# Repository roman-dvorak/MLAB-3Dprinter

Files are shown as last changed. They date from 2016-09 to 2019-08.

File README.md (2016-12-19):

RebeliX
=======
RebeliX – a 3D printer inspired by constructions of Rebel II a Prusa i3. Licensed as GPLv3. Howto and list of materials is available on www.RebeliX.cz (currently only in Czech, we are working on it, help is appreciated).

RebeliX Preview of assembled printer

Build
=====

   sudo pip install stlsort

To continue OpenSCAD has to be installed and available as `openscad` command.

1. Make necessary changes to configuration.scad according to printer that prints the parts and available hardware. 
* Generate a calibration object by `make calibration`.
* Print generated calibration.stl and repeat the steps if unhappy.

When satisfied, run `make clean && make all`. That produces STLs with your tweeks.

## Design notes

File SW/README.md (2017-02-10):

Configuration for Rebelix after editing for MLAB

Configuration.h used to generate printer firmware on these pages:
https://www.repetier.com/firmware/v092/index.php

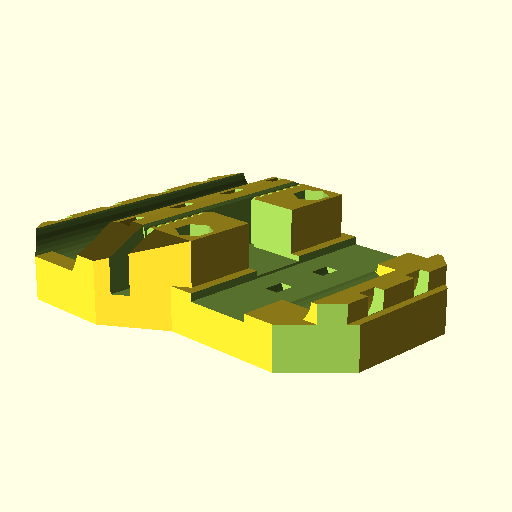
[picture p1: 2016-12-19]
images/x-carriage.png

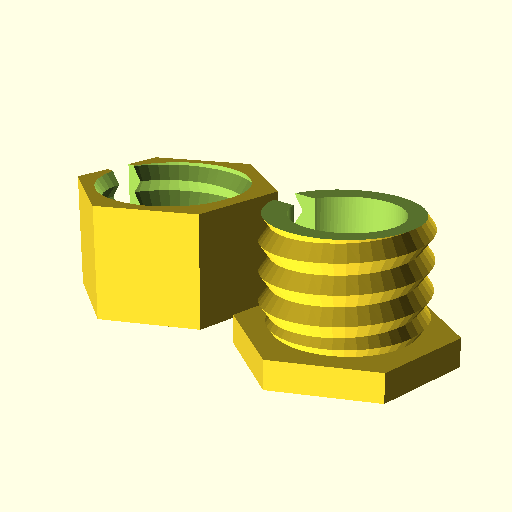
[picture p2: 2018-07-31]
images/filament_cleaner.png

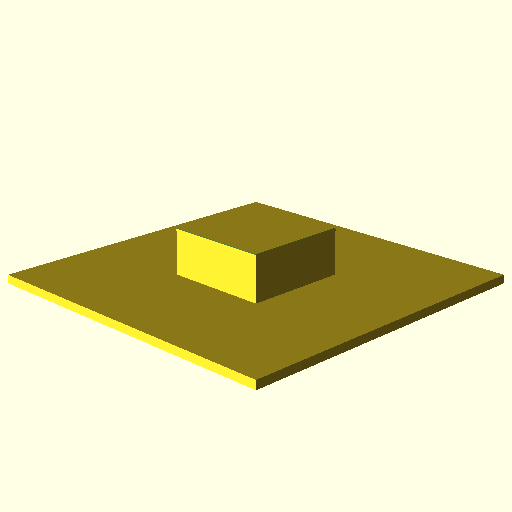
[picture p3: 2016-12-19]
images/profile-cover.png

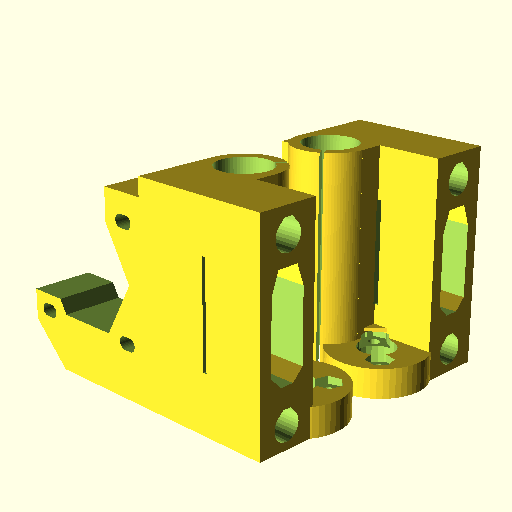
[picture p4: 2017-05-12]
images/x-end-motor.png

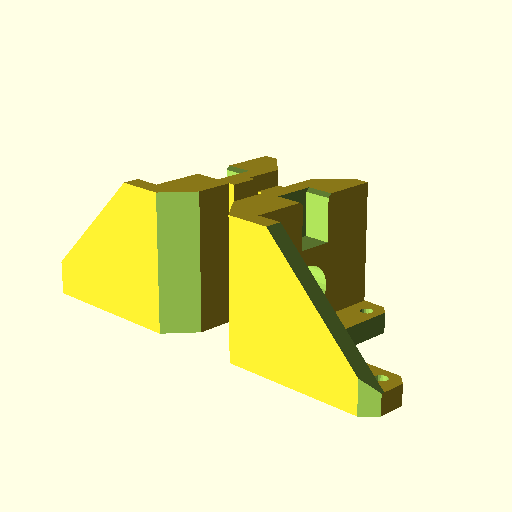
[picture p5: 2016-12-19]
images/z-bottom.png

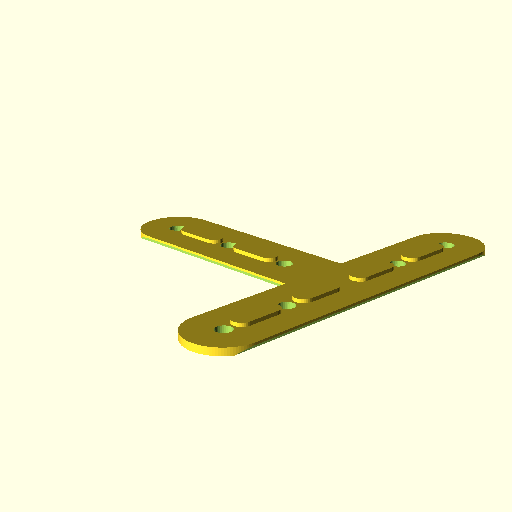
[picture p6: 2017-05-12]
images/z-coupler.png

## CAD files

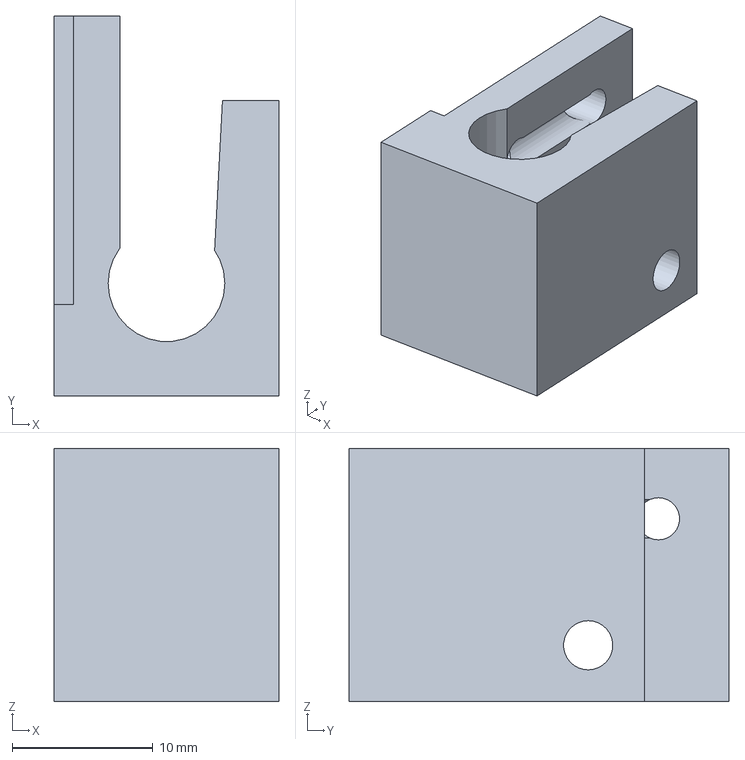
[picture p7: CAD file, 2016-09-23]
gcode/z-endstop-holder.amf
16.0 x 27.0 x 18.0 mm

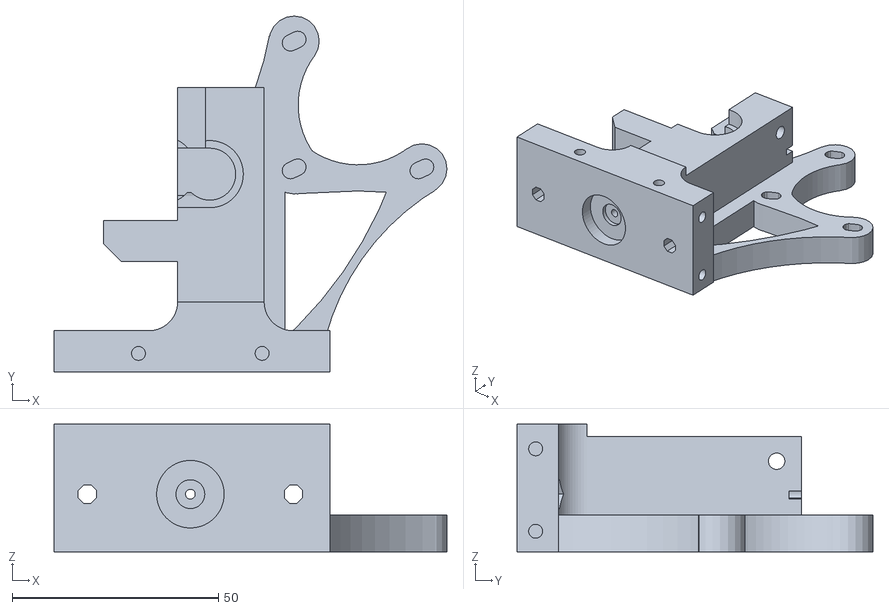
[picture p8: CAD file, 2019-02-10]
src/Extruder_filament_1.75mm/gregs-wade-625.stl
95.4 x 86.4 x 31.0

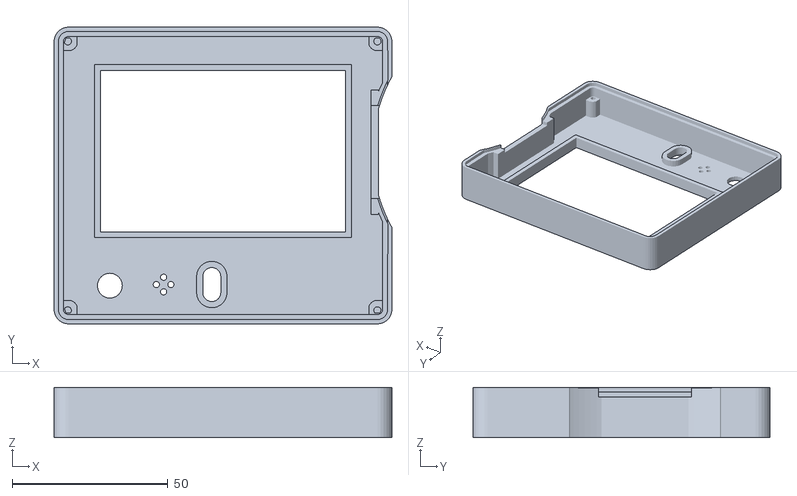
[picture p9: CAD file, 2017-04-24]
STL/LCD_holder/mods_for_display_case_front.stl
108.6 x 95.4 x 16.1

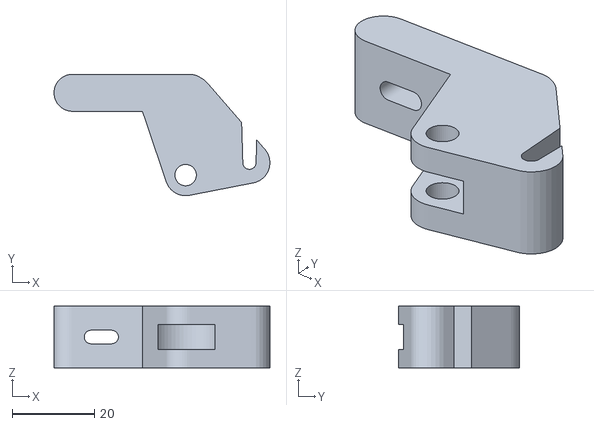
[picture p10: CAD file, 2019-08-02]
STL/MLAB_extruder/extruder_02.stl
52.5 x 29.5 x 15.0

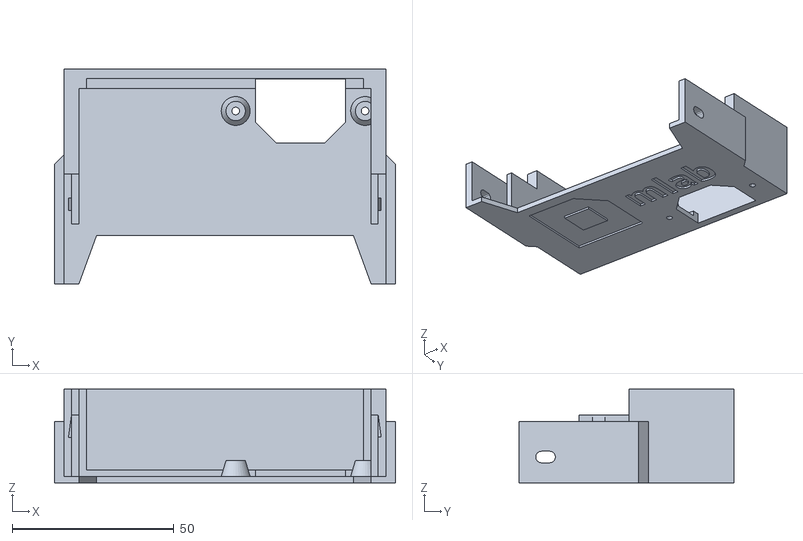
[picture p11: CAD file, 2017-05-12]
STL/Source_cover/Front_EURO_12V_240W.stl
105.4 x 66.5 x 29.0

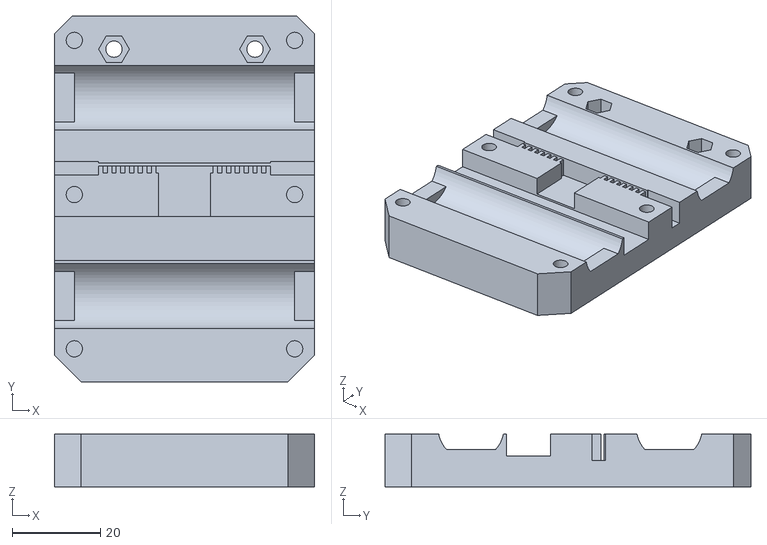
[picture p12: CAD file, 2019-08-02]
STL/x-carriage.stl
59.0 x 83.0 x 12.0

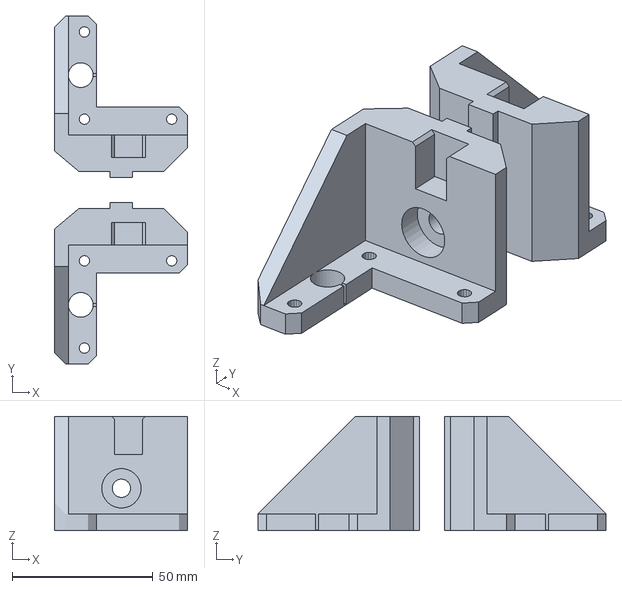
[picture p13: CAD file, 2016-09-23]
gcode/z-bottom.amf
47.3 x 123.6 x 40.6 mm

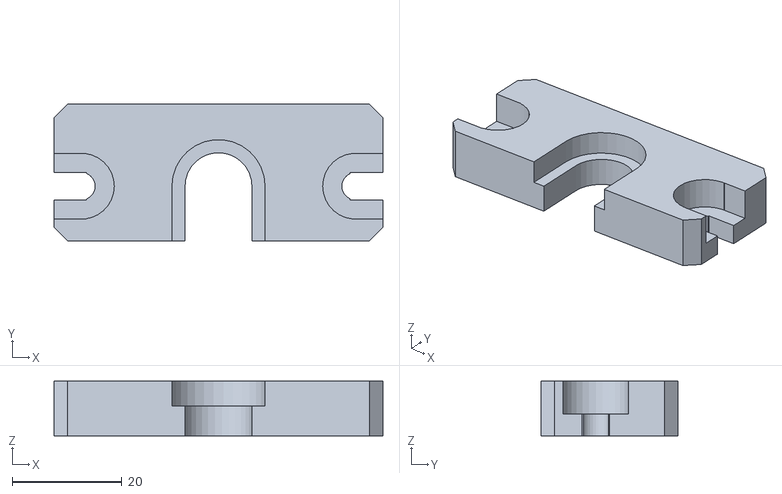
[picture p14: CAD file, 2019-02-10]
STL/Extruder_filament_1.75mm/j-head-mount.stl
60.0 x 25.0 x 10.0

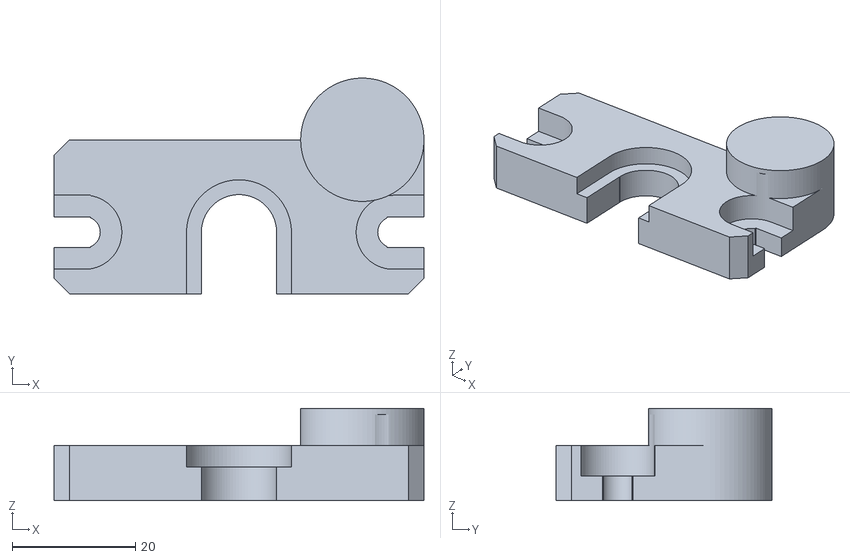
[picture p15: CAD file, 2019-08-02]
STL/j-head-mount.stl
60.0 x 35.0 x 15.0

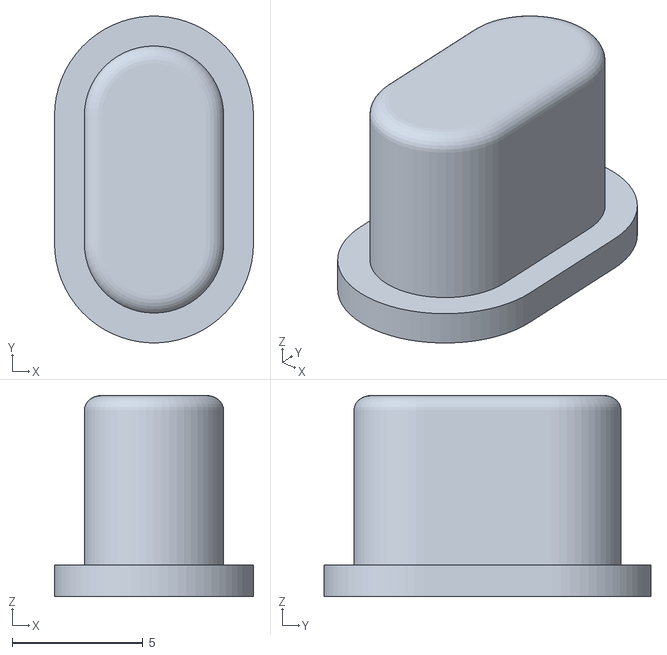
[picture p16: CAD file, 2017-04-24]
STL/LCD_holder/mods_for_display_case_button.stl
7.60 x 12.5 x 7.68

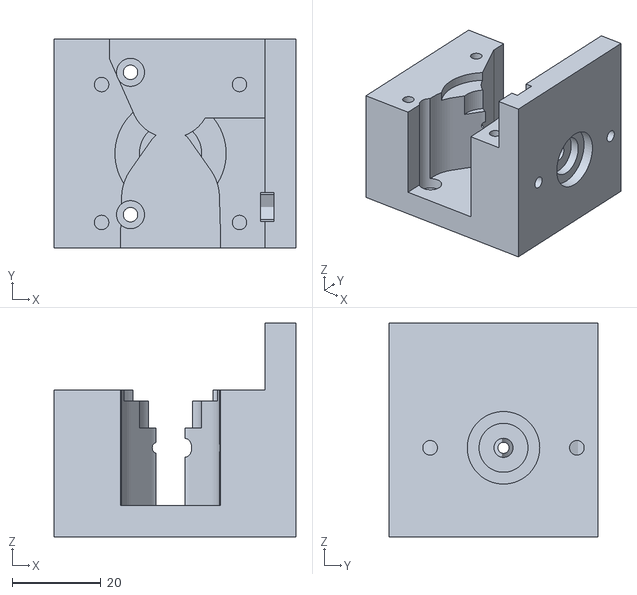
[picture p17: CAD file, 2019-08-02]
STL/MLAB_extruder/extruder_01.stl
54.4 x 46.9 x 48.0

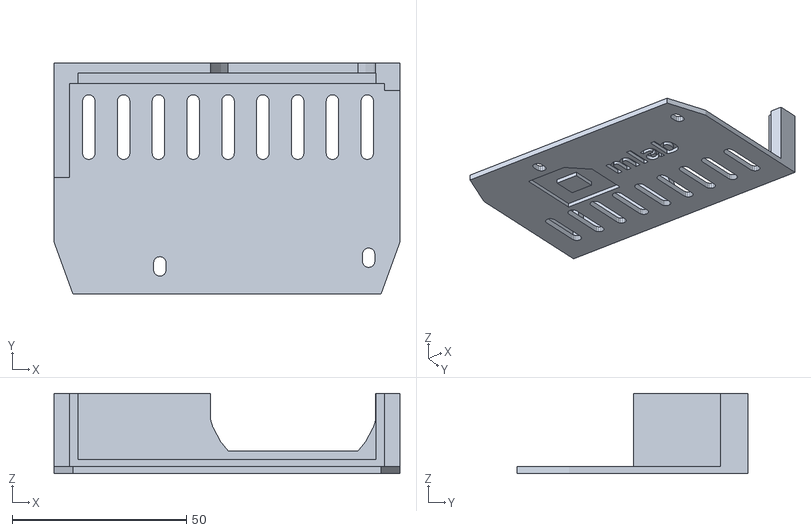
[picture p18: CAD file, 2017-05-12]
STL/Source_cover/Rear_EURO_12V_240W.stl
99.4 x 66.5 x 23.0

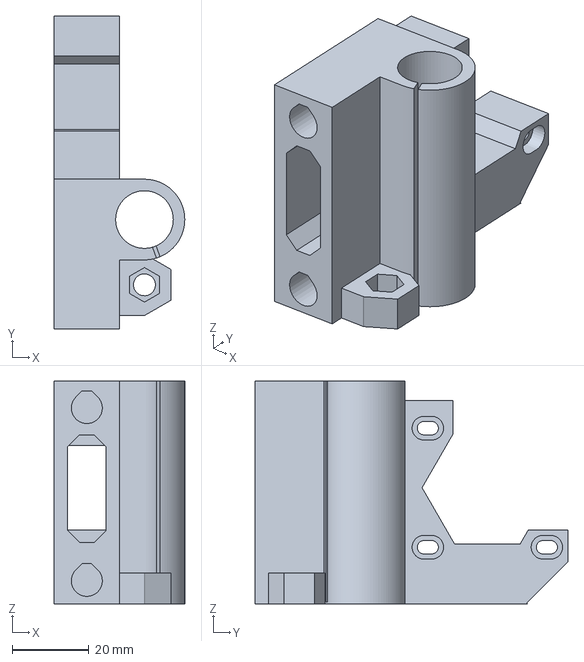
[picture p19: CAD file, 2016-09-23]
gcode/x-end-motor.amf
34.0 x 81.5 x 58.0 mm

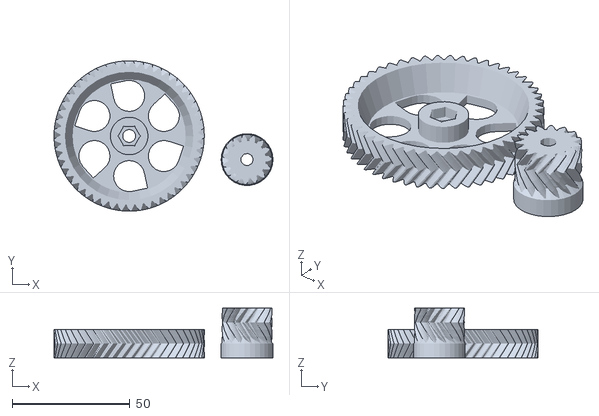
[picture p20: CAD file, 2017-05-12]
STL/Extruder_filament_1.75mm/wade-gears.stl
92.9 x 63.7 x 21.0

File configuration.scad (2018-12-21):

// Layer high for the printing [mm]
layer_height = 0.20; //Slic3r->Print Settings->Layers and perimeters->Layer height

// Spare for the screws heads [mm]
spare = 0.75;
// M6 screw diameter [mm]
M6_head_diameter = 13.6+spare;
//M6_head_diameter = 10.6+spare;
//M6_head_diameter = 12+spare;

// M6 head high (for hiding it) [mm]
//M6_head_height = 4;
M6_head_height = 3.6;
//M6_head_height = 4.5;

// Screws and rods diameters
M8_smooth_rod_diameter = 8.3;
M8_smooth_rod_diameter_catch = 8.4;
// Prumer 8mm tyce
rod_8mm_d = 8.2; //pro dil z-top
M6_diameter = 6.6;
M6_dia=M6_diameter; //pro dil z-top
M6_diamater_horizontal = 6.5;
M3_diameter = 3.7;
M3_diameter_horizontal = 3.5;

//matice trapézové tyče
TRAP_diameter_externa=22; //průmer vnější


// Nuts diameters
M3_nut_diameter = 7.0;
M3_nut_diameter_horizontal = 6.7;

// ALU profile parameters
ALU_cut_width = 7.9;
ALU_cut_width_horizontal = 7.7;

// Sirka matky do profilu (pokud neni pouzita, tak 0)
profile_nut_width = 10;
//profile_nut_width = 0; //pro z-top

// Motors length/depth (for axes Z and Y)
//SX17-1003LQFE (recommended for the Z axis)
motor_length = 29.5;
//SX17-1003 (recommended for the Z axis)
//motor_length = 34;
//SX17-1005
//motor_length = 40;
//SX17-0905 - this motor is too high - the Z end stop holder has to be adjusted
//motor_length = 48;

// Extrusion width [mm]
extrusion_width = 0.66; //Slic3r->Print Settings->Advanced->Default extrusion width

/// Belt type ******************************************************

// GT2
belt_tooth_distance = 2;
belt_tooth_ratio = 0.5;
belt_tooth_height = 1.4;
belt_thickness = 2.3;


// T2.5
//belt_tooth_distance = 2.5;
//belt_tooth_ratio = 0.68;

// Z screw......



// Tloustka rohovych spojek
// 5 mm => sroub M6x14 s podlozkou
// 3 mm => sroub M6x12 s podlozkou
coupler_thickness = 3;

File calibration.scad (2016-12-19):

include <./configuration.scad>

difference(){
	union(){
		cube([36,30,5]);
		translate([0,23,0])cube([35,10,25]);
		translate([M6_diameter*2+8,20,0])cube([ALU_cut_width_horizontal,11,20]);
	}
	translate([M6_diameter,M6_diameter+M3_diameter+5,-1])cylinder(r=M6_diameter/2,h=7,$fn=32);
	translate([M6_diameter,M3_diameter+2,-1]){
		cylinder(r=M3_diameter/2,h=7,$fn=16);	
		translate([0,0,3.5])cylinder(r=M3_nut_diameter/2,h=2.6,$fn=6);
	}
	translate([M6_diameter+M8_smooth_rod_diameter,M8_smooth_rod_diameter+3,layer_height])cylinder(h=7,r=M8_smooth_rod_diameter_catch/2,$fn = 30);
	translate([34.5,M8_smooth_rod_diameter+3,-1])cylinder(h=7,r=M8_smooth_rod_diameter/2,$fn = 30);
	
	translate([M6_diameter+4,34,10]) 
	rotate([90,0,0]){
		cylinder(h = 15, r=M3_diameter_horizontal/2, $fn=30);
		cylinder(h = 4, r=M3_nut_diameter_horizontal/2, $fn=6);
	}

	translate([M6_diameter*2+8+ALU_cut_width/2,34,12]) 
	rotate([90,0,0]){
		cylinder(r = M6_diamater_horizontal/2, h = 15, $fn = 30);
		cylinder(r = M6_head_diameter/2, h = 4, $fn = 30);
	}
	
	translate([-1,27,18.5])belt_holder_beltcut();
}

translate([M6_diameter*2+8,0,0])cube([ALU_cut_width,M6_diameter*2+8,7]);

module belt_holder_beltcut(){
 echo(belt_tooth_ratio*belt_tooth_distance);
 position_tweak=-1.1;
 // Belt slit
 //translate([-66,-0.5+10,3]) 
 translate([0,1.5,0])
 cube([67,0.8,15]);
 // Smooth insert cutout
 //translate([-66,-0.5+10,12]) 
 translate([0,1.5,5])
 rotate([45,0,0]) cube([67,15,15]);
 // Individual teeth
 for ( i = [0 : 23] ){
 	translate([0+i*belt_tooth_distance+position_tweak,0,0]) cube([belt_tooth_ratio*belt_tooth_distance,1.7,15]);
 }
}

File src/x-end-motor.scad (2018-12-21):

    // PRUSA iteration3
// x end motor
// GNU GPL v3
// Josef Průša <iam@josefprusa.cz> and contributors
// http://www.reprap.org/wiki/Prusa_Mendel
// http://prusamendel.org


z_thread_diameter = 12;

include <../configuration.scad>
use <inc/x-end.scad>

module x_end_motor_base(){
 x_end_base();
 translate(v=[-15,31,26.5]) cube(size = [17,44,53], center = true);
}

module x_end_motor_holes(){
 x_end_holes();
 // Position to place
 translate(v=[-1,32,30.25]){
  // Belt hole
  translate(v=[-14,1,0]) cube(size = [10,46,22], center = true);
  // Motor mounting holes
  //translate(v=[20,-15.5,-15.5]) rotate(a=[0,-90,0]) rotate(a=[0,0,90]) cylinder(h = 70, r=1.8, $fn=30);
  //translate(v=[1,-15.5,-15.5]) rotate(a=[0,-90,0]) rotate(a=[0,0,90]) cylinder(h = 10, r=3.1, $fn=30);

  hull(){
    translate(v=[20,-16.5,-15.5]) rotate(a=[0,-90,0]) rotate(a=[0,0,90]) cylinder(h = 70, r=M3_diameter_horizontal/2, $fn=30);
    translate(v=[20,-14.5,-15.5]) rotate(a=[0,-90,0]) rotate(a=[0,0,90]) cylinder(h = 70, r=M3_diameter_horizontal/2, $fn=30);
  }
  hull(){
    translate(v=[1,-16.5,-15.5]) rotate(a=[0,-90,0]) rotate(a=[0,0,90]) cylinder(h = 10, r=3.1, $fn=30);
    translate(v=[1,-14.5,-15.5]) rotate(a=[0,-90,0]) rotate(a=[0,0,90]) cylinder(h = 10, r=3.1, $fn=30);
  }

  hull(){
    translate(v=[20,-16.5,15.5]) rotate(a=[0,-90,0]) rotate(a=[0,0,90]) cylinder(h = 70, r=M3_diameter_horizontal/2, $fn=30);
    translate(v=[20,-14.5,15.5]) rotate(a=[0,-90,0]) rotate(a=[0,0,90]) cylinder(h = 70, r=M3_diameter_horizontal/2, $fn=30);
  }
  hull(){
    translate(v=[1,-16.5,15.5]) rotate(a=[0,-90,0]) rotate(a=[0,0,90]) cylinder(h = 10, r=3.1, $fn=30);
    translate(v=[1,-14.5,15.5]) rotate(a=[0,-90,0]) rotate(a=[0,0,90]) cylinder(h = 10, r=3.1, $fn=30);
  }

  hull(){
    translate(v=[20,16.5,-15.5]) rotate(a=[0,-90,0]) rotate(a=[0,0,90]) cylinder(h = 70, r=M3_diameter_horizontal/2, $fn=30);
    translate(v=[20,14.5,-15.5]) rotate(a=[0,-90,0]) rotate(a=[0,0,90]) cylinder(h = 70, r=M3_diameter_horizontal/2, $fn=30);
  }
  hull(){
    translate(v=[1,16.5,-15.5]) rotate(a=[0,-90,0]) rotate(a=[0,0,90]) cylinder(h = 10, r=3.1, $fn=30);
    translate(v=[1,14.5,-15.5]) rotate(a=[0,-90,0]) rotate(a=[0,0,90]) cylinder(h = 10, r=3.1, $fn=30);
  }

  // Material saving cutout
  translate(v=[-10,12,10]) cube(size = [60,42,42], center = true);

  // Material saving cutout
  translate(v=[-10,40,-30]) rotate(a=[45,0,0])  cube(size = [60,42,42], center = true);
  // Motor shaft cutout
  translate(v=[0,0,0]) rotate(a=[0,-90,0]) rotate(a=[0,0,90+180/8]) cylinder(h = 70, r=17, $fn=8);
  // without motor
  translate(v=[0,-19,0]) rotate(a=[0,-90,0]) rotate(a=[0,0,90]) cylinder(h = 70, d=M3_diameter_horizontal, $fn=60);
  translate(v=[5,-19,0]) rotate(a=[0,-90,0]) rotate(a=[0,0,0]) cylinder(h = 5+8, d=6.4, $fn=6);
  translate(v=[-20,-19,0]) rotate(a=[0,-90,0]) rotate(a=[0,0,0]) cylinder(h = 5+8, d=6.1, $fn=30);
 }
}

// Final part
module x_end_motor(){
 difference(){
  x_end_motor_base();
  x_end_motor_holes();
 }

 translate([30,0,0]) mirror([1,0,0])
   difference(){
   x_end_motor_base();
   x_end_motor_holes();
 }
}

x_end_motor();

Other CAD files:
STL/Extruder_filament_1.75mm/gregs-wade-625.stl
STL/LCD_holder/mods_for_display_case_back.stl
STL/MLAB_extruder/extruder_04.stl
STL/x-carriage-back.stl
src/y-motor.scad
STL/Extruder_filament_1.75mm/extruder-idler.stl
STL/Extruder_filament_1.75mm/extruder-washer.stl
STL/Extruder_filament_1.75mm/extruder_fan.stl
STL/M6_nut_case/M6-case-corner.stl
STL/M6_nut_case/M6-case-dual.stl
STL/M6_nut_case/M6-case-simple.stl
STL/RAMPS_mini.stl
STL/cable-holder-Nema17.stl
STL/cable-holder.stl
STL/corner-coupler.stl
STL/filament_cleaner.stl
STL/heatbed-nut.stl
STL/profile-cover-hole.stl
STL/profile-cover.stl
STL/spool-center.stl
STL/spool-holder.stl
STL/spool_bearing.stl
STL/x-end-motor.stl
STL/y-LM8UU-holder.stl
STL/y-belt-holder.stl
STL/y-motor.stl
STL/y-rod-holder.stl
STL/z-bottom.stl
STL/z-coupler.stl
STL/z-endstop-holder.stl
STL/z-endstop-piezo.stl
STL/z-top.stl
gcode/cable-holder.amf
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

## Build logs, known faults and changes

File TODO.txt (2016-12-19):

Optimalizace modelu pro tisk 

Vyhladit model ozubenych kol. Zvazit modifikaci zubu kola, tak aby nevznikal pri tisku otrep v ozubeni. 

Nastaveni tisku

Snizit mnozstvi vyplne na cca 20%. Asi pouzivat spis typ vyplne Honeycomp, nez reclinear. Honeykomb ma zda se vetsi prispevek k pevnosti.

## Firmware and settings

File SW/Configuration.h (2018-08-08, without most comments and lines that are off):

#define CONFIGURATION_H
#define NUM_EXTRUDER 1
#define MOTHERBOARD 33
#include "pins.h"
#undef FAN_PIN
#define FAN_PIN 9
#undef FAN_BOARD_PIN
#define FAN_BOARD_PIN -1
#define BOARD_FAN_SPEED 255
#define FAN_THERMO_PIN -1
#define FAN_THERMO_MIN_PWM 128
#define FAN_THERMO_MAX_PWM 255
#define FAN_THERMO_MIN_TEMP 45
#define FAN_THERMO_MAX_TEMP 60
#define FAN_THERMO_THERMISTOR_PIN -1
#define FAN_THERMO_THERMISTOR_TYPE 1
#define BLUETOOTH_SERIAL  -1
#define BLUETOOTH_BAUD  115200
#define MIXING_EXTRUDER 0
#define DRIVE_SYSTEM 0
#define XAXIS_STEPS_PER_MM 80
#define YAXIS_STEPS_PER_MM 80
#define ZAXIS_STEPS_PER_MM 408.15
#define EXTRUDER_FAN_COOL_TEMP 50
#define PDM_FOR_EXTRUDER 0
#define PDM_FOR_COOLER 0
#define DECOUPLING_TEST_MAX_HOLD_VARIANCE 20
#define DECOUPLING_TEST_MIN_TEMP_RISE 1
#define KILL_IF_SENSOR_DEFECT 0
#define RETRACT_ON_PAUSE 2
#define PAUSE_START_COMMANDS ""
#define PAUSE_END_COMMANDS ""
#define SHARED_EXTRUDER_HEATER 0
#define EXT0_X_OFFSET 0
#define EXT0_Y_OFFSET 0
#define EXT0_Z_OFFSET 0
#define EXT0_STEPS_PER_MM 514
#define EXT0_TEMPSENSOR_TYPE 14
#define EXT0_TEMPSENSOR_PIN TEMP_0_PIN
#define EXT0_HEATER_PIN HEATER_0_PIN
#define EXT0_STEP_PIN ORIG_E0_STEP_PIN
#define EXT0_DIR_PIN ORIG_E0_DIR_PIN
#define EXT0_INVERSE 1
#define EXT0_ENABLE_PIN ORIG_E0_ENABLE_PIN
#define EXT0_ENABLE_ON 0
#define EXT0_MIRROR_STEPPER 0
#define EXT0_STEP2_PIN ORIG_E0_STEP_PIN
#define EXT0_DIR2_PIN ORIG_E0_DIR_PIN
#define EXT0_INVERSE2 0
#define EXT0_ENABLE2_PIN ORIG_E0_ENABLE_PIN
#define EXT0_MAX_FEEDRATE 50
#define EXT0_MAX_START_FEEDRATE 20
#define EXT0_MAX_ACCELERATION 1000
#define EXT0_HEAT_MANAGER 3
#define EXT0_WATCHPERIOD 1
#define EXT0_PID_INTEGRAL_DRIVE_MAX 250
#define EXT0_PID_INTEGRAL_DRIVE_MIN 100
#define EXT0_PID_PGAIN_OR_DEAD_TIME 2
#define EXT0_PID_I 6
#define EXT0_PID_D 40
#define EXT0_PID_MAX 255
#define EXT0_ADVANCE_K 0
#define EXT0_ADVANCE_L 0
#define EXT0_ADVANCE_BACKLASH_STEPS 0
#define EXT0_WAIT_RETRACT_TEMP 150
#define EXT0_WAIT_RETRACT_UNITS 0
#define EXT0_SELECT_COMMANDS ""
#define EXT0_DESELECT_COMMANDS ""
#define EXT0_EXTRUDER_COOLER_PIN 8
#define EXT0_EXTRUDER_COOLER_SPEED 255
#define EXT0_DECOUPLE_TEST_PERIOD 12000
#define EXT0_JAM_PIN -1
#define EXT0_JAM_PULLUP 0
#define FEATURE_RETRACTION 1
#define AUTORETRACT_ENABLED 0
#define RETRACTION_LENGTH 3
#define RETRACTION_LONG_LENGTH 13
#define RETRACTION_SPEED 40
#define RETRACTION_Z_LIFT 0
#define RETRACTION_UNDO_EXTRA_LENGTH 0
#define RETRACTION_UNDO_EXTRA_LONG_LENGTH 0
#define RETRACTION_UNDO_SPEED 20
#define FILAMENTCHANGE_X_POS 0
#define FILAMENTCHANGE_Y_POS 0
#define FILAMENTCHANGE_Z_ADD  2
#define FILAMENTCHANGE_REHOME 1
#define FILAMENTCHANGE_SHORTRETRACT 5
#define FILAMENTCHANGE_LONGRETRACT 50
#define JAM_STEPS 220
#define JAM_SLOWDOWN_STEPS 320
#define JAM_SLOWDOWN_TO 70
#define JAM_ERROR_STEPS 500
#define JAM_MIN_STEPS 10
#define JAM_ACTION 1
#define RETRACT_DURING_HEATUP true
#define PID_CONTROL_RANGE 10
#define SKIP_M109_IF_WITHIN 2
#define SCALE_PID_TO_MAX 0
#define TEMP_HYSTERESIS 0
#define EXTRUDE_MAXLENGTH 160
#define NUM_TEMPS_USERTHERMISTOR0 0
#define USER_THERMISTORTABLE0 {}
#define NUM_TEMPS_USERTHERMISTOR1 0
#define USER_THERMISTORTABLE1 {}
#define NUM_TEMPS_USERTHERMISTOR2 0
#define USER_THERMISTORTABLE2 {}
#define GENERIC_THERM_VREF 5
#define GENERIC_THERM_NUM_ENTRIES 33
#define HEATER_PWM_SPEED 0
#define HAVE_HEATED_BED 0
#define HEATED_BED_MAX_TEMP 120
#define SKIP_M190_IF_WITHIN 3
#define HEATED_BED_SENSOR_TYPE 14
#define HEATED_BED_SENSOR_PIN TEMP_1_PIN
#define HEATED_BED_HEATER_PIN HEATER_1_PIN
#define HEATED_BED_SET_INTERVAL 5000
#define HEATED_BED_HEAT_MANAGER 3
#define HEATED_BED_PID_INTEGRAL_DRIVE_MAX 255
#define HEATED_BED_PID_INTEGRAL_DRIVE_MIN 80
#define HEATED_BED_PID_PGAIN_OR_DEAD_TIME   2
#define HEATED_BED_PID_IGAIN   18.38
#define HEATED_BED_PID_DGAIN 530.16
#define HEATED_BED_PID_MAX 255
#define HEATED_BED_DECOUPLE_TEST_PERIOD 300000
#define MIN_EXTRUDER_TEMP 150
#define MAXTEMP 248
#define MIN_DEFECT_TEMPERATURE -30
#define MAX_DEFECT_TEMPERATURE 255
#define SUPPORT_LASER 0
#define LASER_PIN -1
#define LASER_ON_HIGH 1
#define SUPPORT_CNC 0
#define CNC_WAIT_ON_ENABLE 300
#define CNC_WAIT_ON_DISABLE 0
#define CNC_ENABLE_PIN -1
#define CNC_ENABLE_WITH 1
#define CNC_DIRECTION_PIN -1
#define CNC_DIRECTION_CW 1
#define DEFAULT_PRINTER_MODE 0
#define ENDSTOP_PULLUP_X_MIN true
#define ENDSTOP_X_MIN_INVERTING false
#define MIN_HARDWARE_ENDSTOP_X true
#define ENDSTOP_PULLUP_Y_MIN true
#define ENDSTOP_Y_MIN_INVERTING false
#define MIN_HARDWARE_ENDSTOP_Y true
#define ENDSTOP_PULLUP_Z_MIN false
#define ENDSTOP_Z_MIN_INVERTING true
#define MIN_HARDWARE_ENDSTOP_Z true
#define ENDSTOP_PULLUP_X_MAX true
#define ENDSTOP_X_MAX_INVERTING false
#define MAX_HARDWARE_ENDSTOP_X false
#define ENDSTOP_PULLUP_Y_MAX true
#define ENDSTOP_Y_MAX_INVERTING false
#define MAX_HARDWARE_ENDSTOP_Y false
#define ENDSTOP_PULLUP_Z_MAX true
#define ENDSTOP_Z_MAX_INVERTING false
#define MAX_HARDWARE_ENDSTOP_Z false
#define max_software_endstop_r true
#define min_software_endstop_x false
#define min_software_endstop_y false
#define min_software_endstop_z false
#define max_software_endstop_x true
#define max_software_endstop_y true
#define max_software_endstop_z true
#define ENDSTOP_X_BACK_MOVE 5
#define ENDSTOP_Y_BACK_MOVE 5
#define ENDSTOP_Z_BACK_MOVE 10
#define ENDSTOP_X_RETEST_REDUCTION_FACTOR 2
#define ENDSTOP_Y_RETEST_REDUCTION_FACTOR 2
#define ENDSTOP_Z_RETEST_REDUCTION_FACTOR 0
#define ENDSTOP_X_BACK_ON_HOME 1
#define ENDSTOP_Y_BACK_ON_HOME 1
#define ENDSTOP_Z_BACK_ON_HOME 0
#define ALWAYS_CHECK_ENDSTOPS 1
#define X_ENABLE_ON 0
#define Y_ENABLE_ON 0
#define Z_ENABLE_ON 0
#define DISABLE_X 0
#define DISABLE_Y 0
#define DISABLE_Z 1
#define DISABLE_E 0
#define INVERT_X_DIR 0
#define INVERT_Y_DIR 1
#define INVERT_Z_DIR 0
#define X_HOME_DIR -1
#define Y_HOME_DIR -1
#define Z_HOME_DIR -1
#define X_MAX_LENGTH 185
#define Y_MAX_LENGTH 180
#define Z_MAX_LENGTH 185
#define X_MIN_POS 0
#define Y_MIN_POS 0
#define Z_MIN_POS 0
#define DISTORTION_CORRECTION 1
#define DISTORTION_CORRECTION_POINTS 5
#define DISTORTION_CORRECTION_R 100
#define DISTORTION_PERMANENT 1
#define DISTORTION_UPDATE_FREQUENCY 15
#define DISTORTION_START_DEGRADE 0.5
#define DISTORTION_END_HEIGHT 1
#define DISTORTION_EXTRAPOLATE_CORNERS 0
#define DISTORTION_XMIN 10
#define DISTORTION_YMIN 10
#define DISTORTION_XMAX 190
#define DISTORTION_YMAX 190
#define FEATURE_BABYSTEPPING 1
#define BABYSTEP_MULTIPLICATOR 80
#define DELTA_SEGMENTS_PER_SECOND_PRINT 180 // Move accurate setting for print moves
#define DELTA_SEGMENTS_PER_SECOND_MOVE 70 // Less accurate setting for other moves
#define EXACT_DELTA_MOVES 1
#define DELTA_HOME_ON_POWER 0
#define DELTASEGMENTS_PER_PRINTLINE 24
#define STEPPER_INACTIVE_TIME 360L
#define MAX_INACTIVE_TIME 0L
#define MAX_FEEDRATE_X 80
#define MAX_FEEDRATE_Y 80
#define MAX_FEEDRATE_Z 30
#define HOMING_FEEDRATE_X 50
#define HOMING_FEEDRATE_Y 50
#define HOMING_FEEDRATE_Z 15
#define HOMING_ORDER HOME_ORDER_XYZ
#define ZHOME_MIN_TEMPERATURE 0
#define ZHOME_HEAT_ALL 1
#define ZHOME_HEAT_HEIGHT 20
#define ZHOME_X_POS 999999
#define ZHOME_Y_POS 999999
#define ENABLE_BACKLASH_COMPENSATION 0
#define X_BACKLASH 0
#define Y_BACKLASH 0
#define Z_BACKLASH 0
#define RAMP_ACCELERATION 1
#define STEPPER_HIGH_DELAY 1
#define DIRECTION_DELAY 0
#define STEP_DOUBLER_FREQUENCY 12000
#define ALLOW_QUADSTEPPING 1
#define DOUBLE_STEP_DELAY 1 // time in microseconds
#define MAX_ACCELERATION_UNITS_PER_SQ_SECOND_X 1000
#define MAX_ACCELERATION_UNITS_PER_SQ_SECOND_Y 1000
#define MAX_ACCELERATION_UNITS_PER_SQ_SECOND_Z 500
#define MAX_TRAVEL_ACCELERATION_UNITS_PER_SQ_SECOND_X 1000
#define MAX_TRAVEL_ACCELERATION_UNITS_PER_SQ_SECOND_Y 1000
#define MAX_TRAVEL_ACCELERATION_UNITS_PER_SQ_SECOND_Z 500
#define INTERPOLATE_ACCELERATION_WITH_Z 0
#define ACCELERATION_FACTOR_TOP 100
#define MAX_JERK 30
#define MAX_ZJERK 0.3
#define PRINTLINE_CACHE_SIZE 16
#define MOVE_CACHE_LOW 10
#define LOW_TICKS_PER_MOVE 250000
#define EXTRUDER_SWITCH_XY_SPEED 100
#define DUAL_X_AXIS 0
#define FEATURE_TWO_XSTEPPER 0
#define X2_STEP_PIN   ORIG_E1_STEP_PIN
#define X2_DIR_PIN    ORIG_E1_DIR_PIN
#define X2_ENABLE_PIN ORIG_E1_ENABLE_PIN
#define FEATURE_TWO_YSTEPPER 0
#define Y2_STEP_PIN   ORIG_E1_STEP_PIN
#define Y2_DIR_PIN    ORIG_E1_DIR_PIN
#define Y2_ENABLE_PIN ORIG_E1_ENABLE_PIN
#define FEATURE_TWO_ZSTEPPER 0
#define Z2_STEP_PIN   ORIG_E1_STEP_PIN
#define Z2_DIR_PIN    ORIG_E1_DIR_PIN
#define Z2_ENABLE_PIN ORIG_E1_ENABLE_PIN
#define FEATURE_THREE_ZSTEPPER 0
#define Z3_STEP_PIN   ORIG_E2_STEP_PIN
#define Z3_DIR_PIN    ORIG_E2_DIR_PIN
#define Z3_ENABLE_PIN ORIG_E2_ENABLE_PIN
#define FEATURE_DITTO_PRINTING 0
#define USE_ADVANCE 0
#define ENABLE_QUADRATIC_ADVANCE 0
#define BAUDRATE 115200
#define ENABLE_POWER_ON_STARTUP 0
#define POWER_INVERTING 0
#define KILL_METHOD 1
#define ACK_WITH_LINENUMBER 1
#define WAITING_IDENTIFIER "wait"
#define ECHO_ON_EXECUTE 1
#define EEPROM_MODE 1
#undef PS_ON_PIN
#define PS_ON_PIN -1
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

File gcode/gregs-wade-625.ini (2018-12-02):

top_solid_layers = 4
top_solid_infill_speed = 33
top_infill_pattern = rectilinear
top_infill_extrusion_width = 0
thin_walls = 1
solid_infill_speed = 50
solid_infill_extrusion_width = 0
solid_infill_extruder = 1
solid_infill_every_layers = 0
solid_infill_below_area = 30
small_perimeter_speed = 33
perimeters = 2
perimeter_speed = 80
perimeter_extrusion_width = 0
perimeter_extruder = 1
overhangs = 1
min_top_bottom_shell_thickness = 0
min_shell_thickness = 0
infill_speed = 90
infill_overlap = 55%
infill_extrusion_width = 250%
infill_extruder = 1
infill_every_layers = 1
gap_fill_speed = 35
fill_pattern = honeycomb
fill_gaps = 1
fill_density = 7%
fill_angle = 45
extra_perimeters = 1
external_perimeters_first = 0
external_perimeter_speed = 60%
external_perimeter_extrusion_width = 0
bridge_speed = 60
bridge_flow_ratio = 1
bottom_solid_layers = 4
bottom_infill_pattern = rectilinear
xy_size_compensation = 0
support_material_threshold = 60%
support_material_speed = 60
support_material_spacing = 2.5
support_material_pillar_spacing = 10
support_material_pillar_size = 2.5
support_material_pattern = pillars
support_material_max_layers = 0
support_material_interface_speed = 100%
support_material_interface_spacing = 0
support_material_interface_layers = 3
support_material_interface_extrusion_width = 0
support_material_interface_extruder = 1
support_material_extrusion_width = 0
support_material_extruder = 1
support_material_enforce_layers = 0
support_material_contact_distance = 0.2
support_material_buildplate_only = 0
support_material_angle = 0
support_material = 0
sequential_print_priority = 0
seam_position = aligned
regions_overlap = 0
raft_layers = 0
match_horizontal_surfaces = 0
layer_height = 0.2
interface_shells = 0
infill_only_where_needed = 0
first_layer_height = 0.3
extrusion_width = 0
dont_support_bridges = 1
adaptive_slicing_quality = 75%
adaptive_slicing = 0
z_steps_per_mm = 0
z_offset = 0
wipe = 0
vibration_limit = 0
use_volumetric_e = 0
use_set_and_wait_extruder = 0
use_set_and_wait_bed = 0
use_relative_e_distances = 0
use_firmware_retraction = 0
travel_speed = 130
toolchange_gcode = 
threads = 4
temperature = 213
start_gcode = M355 S1; rozsvitit\nG28 ; home all axes\nG1 Z5 F5000 ; lift nozzle
start_filament_gcode = "; Filament gcode\n"
standby_temperature_delta = -5
spiral_vase = 0
slowdown_below_layer_time = 5
skirts = 1
skirt_height = 1
skirt_distance = 6
retract_speed = 40
retract_restart_extra_toolchange = 0
retract_restart_extra = 0
retract_lift_below = 0
retract_lift_above = 0
retract_lift = 0
retract_length_toolchange = 10
retract_length = 2.5
retract_layer_change = 1
retract_before_travel = 2
resolution = 0
printer_notes = 
pressure_advance = 0
post_process = 
perimeter_acceleration = 0
output_filename_format = [input_filename_base].gcode
ooze_prevention = 0
only_retract_when_crossing_perimeters = 1
nozzle_diameter = 0.4
notes = 
min_skirt_length = 0
min_print_speed = 10
min_layer_height = 0.15
min_fan_speed = 20
max_volumetric_speed = 0
max_print_speed = 80
max_layer_height = 0.3
max_fan_speed = 35
layer_gcode = 
label_printed_objects = 0
interior_brim_width = 0
infill_first = 0
infill_acceleration = 0
has_heatbed = 1
gcode_flavor = repetier
gcode_comments = 0
gcode_arcs = 0
first_layer_temperature = 213
first_layer_speed = 22
first_layer_extrusion_width = 200%
first_layer_bed_temperature = 40
first_layer_acceleration = 0
filament_notes = ""
filament_max_volumetric_speed = 0
filament_diameter = 1.75
filament_density = 1.75
filament_cost = 800
filament_colour = #FFFFFF
fan_below_layer_time = 60
fan_always_on = 0
extrusion_multiplier = 1
extrusion_axis = E
extruder_offset = 0x0
extruder_clearance_radius = 20
extruder_clearance_height = 20
end_gcode = M104 S0 ; turn off temperature\nG28 X0  ; home X axis\nM84     ; disable motors\nM355 S0
end_filament_gcode = "; Filament-specific end gcode \n;END gcode for filament\n"
duplicate_distance = 6
disable_fan_first_layers = 2
default_acceleration = 0
cooling = 1
complete_objects = 0
brim_width = 0
brim_connections_width = 0
bridge_fan_speed = 40
bridge_acceleration = 0
between_objects_gcode = 
before_layer_gcode = 
bed_temperature = 40
bed_shape = 0x0,200x0,200x200,0x200
avoid_crossing_perimeters = 1

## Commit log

2015-06-11 make belt holder more printable.
    [y-belt-holder.scad]
2015-06-11 Parts modified for symplification of the printing and assembling process. Belt slits modified to aline teeth edges to printed wall of the parts.
    [configuration.scad, corner-coupler.amf, extruder-idler.amf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]
2015-07-31 Model optimalisation for better printing on low quality printers.
    [corner-coupler.amf, x-end-idler.amf, y-belt-holder.amf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]
2016-09-23 Slic3r configuration improved for more stable printing.
    [cable-holder.amf, calibration.amf, profile-cover.amf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]
2016-12-19 Improve printability of models
    [gregs-wade-625.stl, wade-gears.scad, wade-gears.stl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]
2016-12-19 repository cleanup.
    [calibration.amf, calibration.stl]
2016-12-19 removed unnecessary G-codes and configuration modified.
    [configuration.scad]
2016-12-19 Unecessarry M8_smooth_rod_diameter_catch parameter removed.
    [calibration.scad, configuration.scad]
2016-12-19 Calibration model fixed.
    [calibration.scad]
2016-12-19 STL files regenerated by makefile.
    [RAMPS_mini.stl, belt-guide.stl, cable-holder.stl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]
2016-12-19 new calibration STL model generated according to modified diameter of rods.
    [calibration.scad, calibration.stl]
2016-12-19 Icreased margin for smooth rods.
    [calibration.scad, calibration.stl, configuration.scad]
2016-12-19 Related STL regerated according to change of rod diameter.
    [calibration.stl, y-rod-holder.stl, z-bottom.stl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]
2016-12-19 X, Y idlers removed and replaced by tandem motor.
    [cable-holder-Nema17.scad, cable-holder-Nema17.stl, x-end-idler.scad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]
2017-02-10 New
    Piezo holder, configuration for firmawe
    [Configuration.h, polyScrewThread_r1.scad, polytests.scad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]
2017-02-10 New z-coupler
    [z-coupler.scad]
2017-02-13 Edit z-coupler
    [MLAB_logo.scad, z-coupler.scad, z-coupler.stl]
2017-02-13 New 35mm endstop
    [z-endstop-piezo.scad, z-endstop-piezo_35mm.stl]
2017-02-14 extrude fan and filament cleaner
    [extruder_fan.scad, extruder_fan.stl, filament_cleaner.scad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]
2017-04-24 New componets
    source cower, lcd holder,
    [Case_for_the_Full_Graphic_Smart_LCD-Top_Case_FGD.stl, Case_for_the_Full_Graphic_Smart_LCD_Controller-Bottom_Case_FGD.stl, Front_EURO_12V_240W.scad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]
2017-04-24 Move stl
    [Front_EURO_12V_240W.stl, Rear_EURO_12V_240W.stl, mods_for_display_case_back.stl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]
2017-05-12 Regeneratig STL files.
    [Case_for_the_Full_Graphic_Smart_LCD-Top_Case_FGD.stl, Case_for_the_Full_Graphic_Smart_LCD_Controller-Bottom_Case_FGD.stl, Front_EURO_12V_240W.stl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]
2017-05-12 gears merged in to one STL.
    [wade-gears.scad, wade-gears.stl]
2017-05-12 obsolete files removed.
    [x-end-idler.scad]
2017-06-05 New components
    [M6-case-corner.stl, M6-case-dual.stl, M6-case-simple.stl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]
2017-10-20 Reverting jacho changes in wade gears.
    [wade-gears.scad]
2017-10-20 Rendering STL with fix of missing screw.
    [wade-gears.scad]
2018-07-31 Přerenderování STL souborů.
    [RAMPS_mini.stl, cable-holder-Nema17.stl, cable-holder.stl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]
2018-08-08 Posledni verze nastaveni.
    [Configuration.h]
2018-12-02 small edits ... dimensions, shapes, ..
    [configuration.scad, gregs-wade-625.scad, gregs-wade-625.stl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]
2018-12-21 upravy rozmeru
    [configuration.scad, gregs-wade-625.scad, x-carriage.scad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]
2019-02-10 Extruder new mounting hole, change dimensions, new back part of X-carriage.
    [assembly.scad, bearing.scad, extruder_model.scad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]
2019-05-22 Vytvoření sestavy
    [assembly.scad, extruder.scad]
2019-05-22 Uprava voziku osy X
    [x-carriage-back.scad, x-carriage.scad]
2019-08-02 Uprava drzaku HE
    [assembly.scad, extruder.scad, extruder_01.stl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]

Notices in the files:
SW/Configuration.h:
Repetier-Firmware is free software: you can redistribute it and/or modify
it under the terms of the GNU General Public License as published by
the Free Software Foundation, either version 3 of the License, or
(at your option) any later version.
